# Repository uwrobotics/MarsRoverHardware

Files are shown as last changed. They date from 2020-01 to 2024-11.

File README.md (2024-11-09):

# University of Waterloo Mars Rover Hardware Repository

## Getting Started

1. Download free student license from [Altium](https://www.altium.com/solutions/academic-programs/student-licenses)
2. Download [Saturn PCB Toolkit](http://www.saturnpcb.com/pcb_toolkit/)

## Best Practices and Tips
- Preface your commit message with the project name in all caps. For example "ARM: add TVS diode" or "LIBRARY: add 10K 0603 resistor"
- When modifying the libraries, notify the #ee-git Discord channel 
- Please read this article on writing good commit messages: https://chris.beams.io/posts/git-commit/

## System Block Diagram
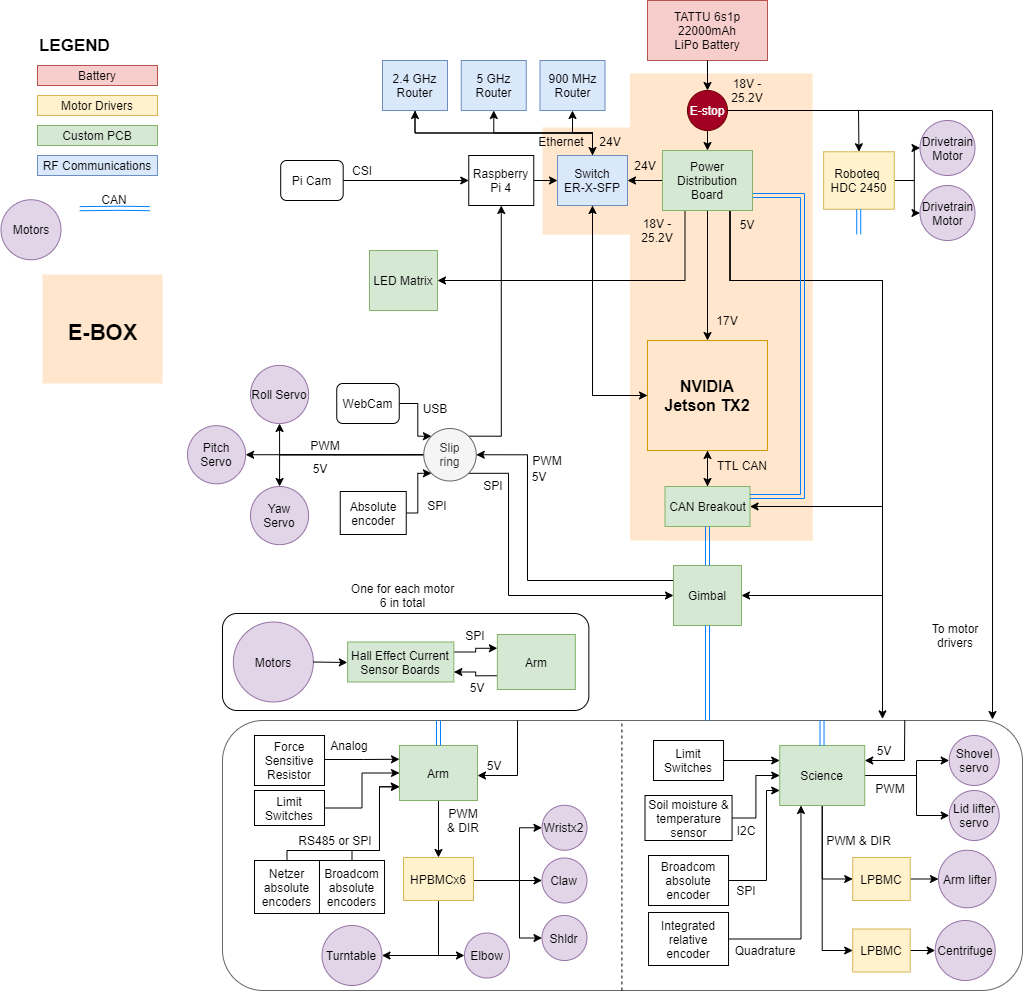
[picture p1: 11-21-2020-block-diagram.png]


#TODO: UPDATE THIS DOCUMENT
test

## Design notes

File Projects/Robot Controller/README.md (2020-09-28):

# Robot Controller

The new Robot Controller board(s) will be responsible for replacing the XBox360 Controller currently used to control the rover. As it stands now, the current plans are to design 3 boards which will each control certain modules of the rover, and can be connected/disconnected at any time. A Dev Board has been created in order to test out different control components and see which are preferred. The MCU which will be on each board is the [STM32F446RET6](https://www.st.com/resource/en/datasheet/stm32f446re.pdf).

## Block Diagram

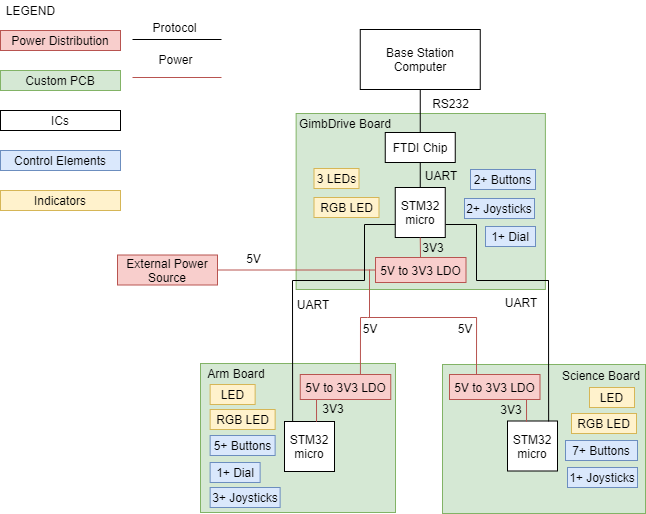
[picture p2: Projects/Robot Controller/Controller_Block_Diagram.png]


## Contributors

* **Christopher Arjune** - *Schematic Design* - [ChristopherA057](https://github.com/ChristopherA057)
* **Qinyang Bao** - *Schematic Design* - [Q7bao](https://github.com/qinyang-bao)

## Built With

* [Altium Designer](https://www.altium.com/) - PCB design software used

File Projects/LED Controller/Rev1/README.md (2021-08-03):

# LED Controller Board

The LED Controller board...

## Block Diagram

## Images

## Designers

* **Ari Wasch** - *Schematic Capture and PCB design* - [ariwasch](https://github.com/ariwasch)

## Built With

* [Altium Designer](https://www.altium.com/) - The PCB design software used

## Errata

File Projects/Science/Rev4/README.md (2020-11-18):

# Science Board

The science board is responsible for interfacing with the motors, servos, and sensors in the rover's science data collection module.
The science module consists of two primary components; the digger used to collect soil samples and the centrifuge used to mix soil samples with chemicals 
The science module will test the dampness of soil sites using the STEMMA moisture sensor to determine where to retreive soil samples.
The digger has two sub-modules the scoop and the lift.
The scoop uses the Hitec HS-82MG servo to collect soil samples.
The lift raises and lowers the scoop using a Pololu 4695.
At the top of the lift the sample into the centrifuge.
The centrifuge consists of two components; the lid and the geniva drive used to rotate the centrifuge.
The lid is controlled by the Feetech FS90 servo.
The geniva drive is driven by Pololu 4685.

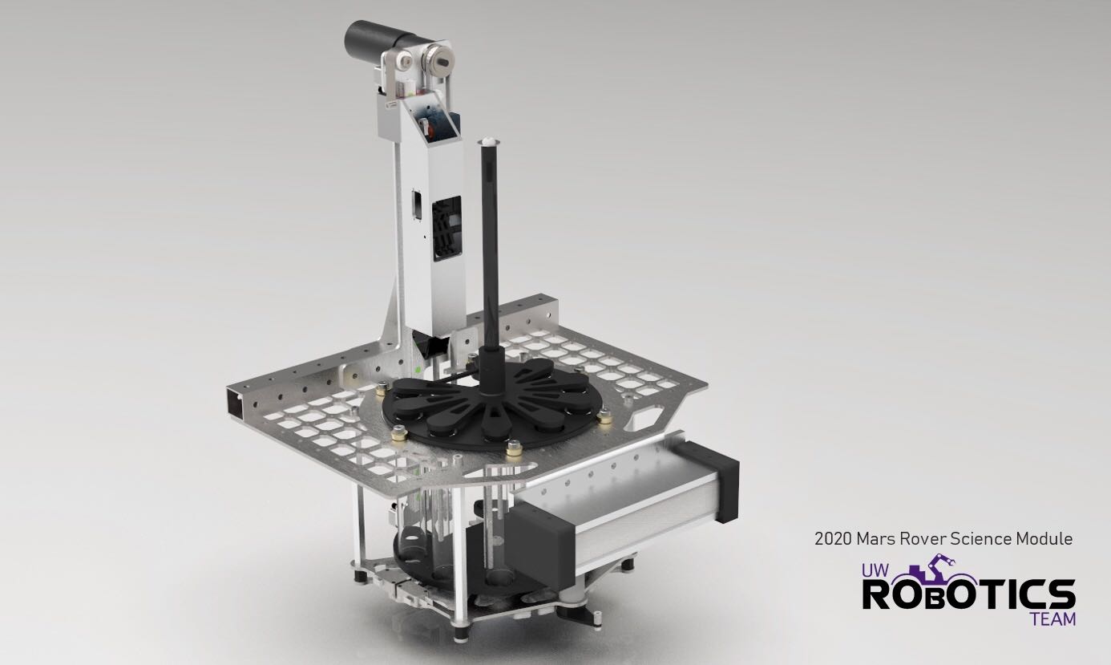
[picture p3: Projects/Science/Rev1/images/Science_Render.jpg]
Science_Render


## Block Diagram

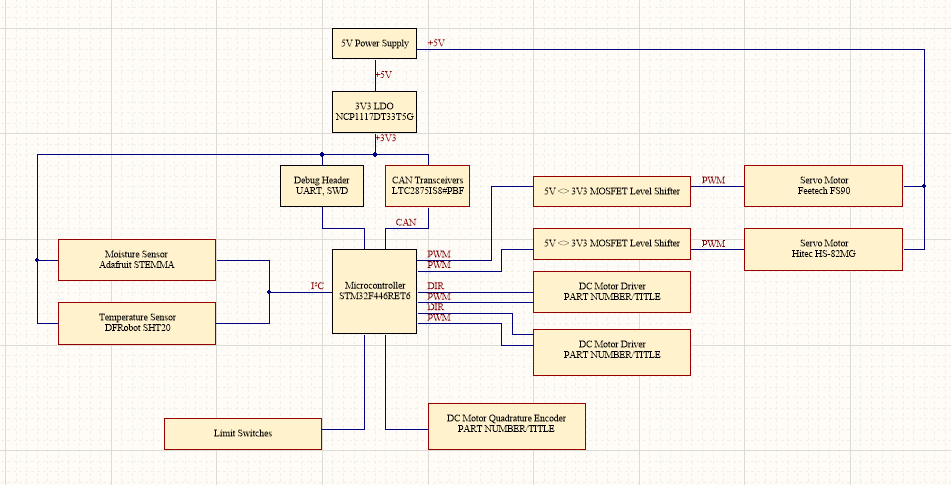
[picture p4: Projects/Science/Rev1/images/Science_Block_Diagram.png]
Block Diagram


## Actuators

### Motor Controllers

* [Cytron 10A 5-30V Dual Channel DC Motor Driver](https://www.robotshop.com/ca/en/cytron-10a-5-30v-dual-channel-dc-motor-driver.html)

### Servos

* [Feetech FS90](https://www.pololu.com/product/2818) - 9g analog servo
* [Hitec HS-82MG](https://hitecrcd.com/products/servos/micro-and-mini-servos/analog-micro-and-mini-servos/hs-82mg/product) - Metal gear micro servo 

### Motors

* [Pololu 4693 motor](https://www.pololu.com/product/4693)
* [Pololu 4685 motor](https://www.pololu.com/product/4685)

## Sensors

* [Adafruit STEMMA Soil Sensor](https://www.adafruit.com/product/4026) - I2C capacitive moisture sensor

## Images

## Designers

* **Wolfgang Windholtz** - *Schematic and PCB design* - [WolfgangWindholtz](https://github.com/WolfgangWindholtz)

## Built With

* [Altium Designer](https://www.altium.com/) - The PCB design software used

## Errata

* TBD

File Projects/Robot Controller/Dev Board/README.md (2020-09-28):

# Robot Controller - Dev Board

The Robot Controller Dev Board was created for the purpose of testing various possible components for the real Robot Controller, as well as various subsystems like power delivery and serial communication over USB. Some components on the board include joysticks, buttons, switches, and potentiometers. The MCU used on the board is the [STM32F446RET6](https://www.st.com/resource/en/datasheet/stm32f446re.pdf).

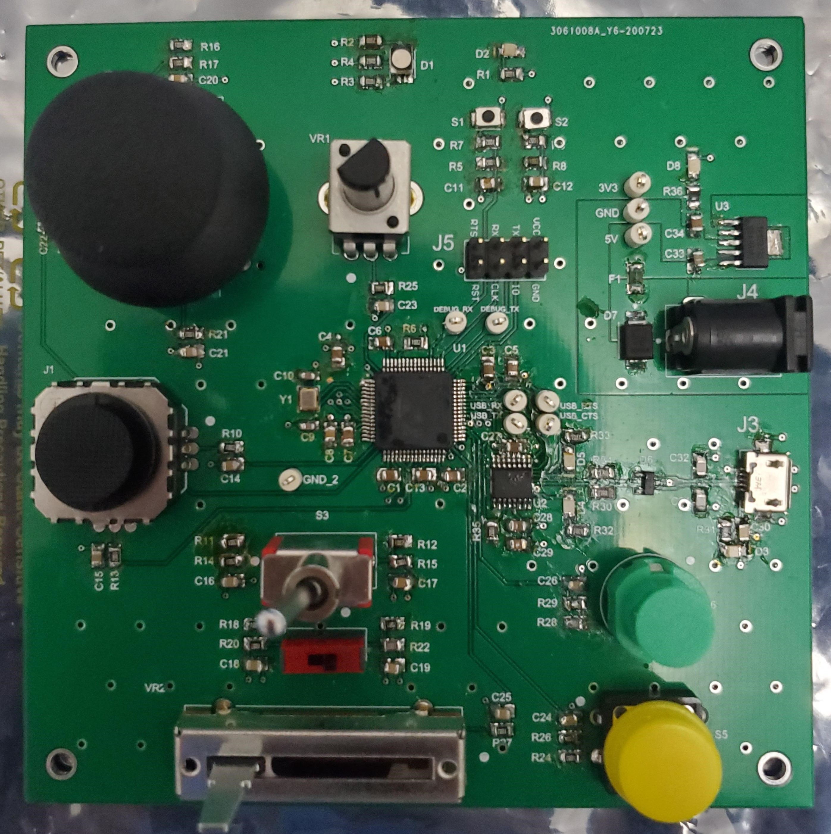
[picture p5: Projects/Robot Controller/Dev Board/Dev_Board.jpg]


## Peripherals

### Joysticks

* [COM-09032 Joystick](https://www.sparkfun.com/products/9032) - 10 kOhm 2-Axis Joystick (PS2-Style)
* [2765 Mini Joystick](https://www.adafruit.com/product/2765) - 10 kOhm 2-Axis Joystick (PSP-Style)

### Buttons

* [COM-10302 Buttons](https://www.sparkfun.com/products/10302) - 12 Tactile Buttons
* [D6R50 F2 Button](https://www.digikey.ca/en/products/detail/c-k/D6R50-F2-LFS/1466350) - Tactile Button

### Switches

* [SPDT Switch](https://www.digikey.ca/en/products/detail/e-switch/100SP1T1B4M2QE/378824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) - Toggle SPDT Switch
* [Mini SPDT Switch](https://www.digikey.ca/en/products/detail/nkk-switches/SS12SDP2/1014829) - Toggle SPDT Switch (but smaller)

### Potentiometers

* [Rotary Potentiometer](https://www.digikey.ca/en/products/detail/bourns-inc/PTV09A-4020F-B103/3534181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) - 10 kOhm Potentiometer (Rotary)
* [Slide Potentiometer](https://www.digikey.ca/en/products/detail/bourns-inc/PTA2043-2015DPB103/3781179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) - 10 kOhm Potentiomer (Slide)

## Contributors

* **Christopher Arjune** - *Schematic Design* - [ChristopherA057](https://github.com/ChristopherA057)
* **Qinyang Bao** - *Schematic Design* - [Q7bao](https://github.com/qinyang-bao)

## Built With

* [Altium Designer](https://www.altium.com/) - PCB design software used

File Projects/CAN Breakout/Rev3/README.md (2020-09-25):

# CAN Breakout Board

This board is resonsible for...

## Block Diagram

## Peripherals

## Images

## Designers

* **Qinyang Bao** - *Schematic and PCB Design* - [qinyang-bao](https://github.com/qinyang-bao)
* **Christopher Arjune** - *Schematic and PCB Design* - [ChristopherA057](https://github.com/ChristopherA057)

## Built With

* [Altium Designer](https://www.altium.com/) - The PCB design software used
* [OSHStencils](https://www.oshstencils.com/) - The PCB stencil maker used

## Errata

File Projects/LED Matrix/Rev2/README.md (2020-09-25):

# LED Matrix

This board is resonsible for...

## Block Diagram

## Peripherals

### LED 

### MOSFETs

## Images

## Designers

* **Emily Adam** - *Schematic and PCB Design* - [adamemily](https://github.com/adamemily)

## Built With

* [Altium Designer](https://www.altium.com/) - The PCB design software used
* [OSHStencils](https://www.oshstencils.com/) - The PCB stencil maker used

## Errata

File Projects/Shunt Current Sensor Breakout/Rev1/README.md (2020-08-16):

# Current Sensor Board

The current sensor board is used to ensure the measured device is operating under optimal conditions and to detect erroneous behaviour to protect components.

## Current Sensor 

* [Texas Instruments INA226](https://www.ti.com/product/INA226) - 36V, 16-bit, ultra-precise i2c output current/voltage/power monitor w/alert

## Images
Assembled PCB:
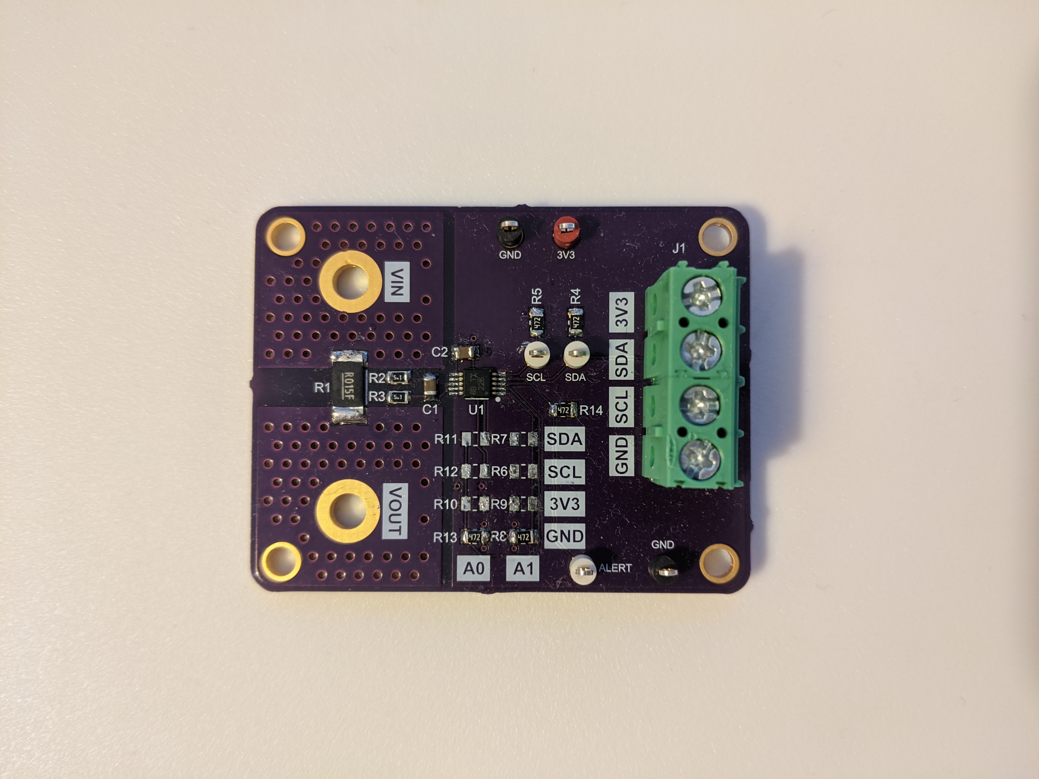
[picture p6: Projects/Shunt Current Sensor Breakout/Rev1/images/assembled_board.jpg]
Assembled PCB


## Designers

* **Noah Chapman** - *Schematic capture and PCB design* - [Nzyme](https://github.com/Nzyme)
* **Kyle Hong** - *PCB design* - [Scotrus](https://github.com/Scotrus)

## Built With

* [Altium Designer](https://www.altium.com/) - The PCB design software used

## Errata

* TBD

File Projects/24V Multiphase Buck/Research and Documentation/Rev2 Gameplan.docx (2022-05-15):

# Multiphase Buck Game Plan

## Problems/Changes

- IC power dissipation is too high
  - Can relieve this by either going down to 1 FET and a slightly lower frequency
  - Or by using a FET with a lower QGate
- Thermal reliefs on small passives are too thick
- Add in a way to break open each channel to measure output current
- Currently IC power losses may be making up the majority of power losses on the board.
- New FET – should only need one, place footprints for two
- New output caps – need low ESR ceramic
  - Need to be stable at intended temperature and frequency
  - Check temperature rise due to self heating by calculating capacitor rms current
- Double check all datasheet calculations
- Re-do datasheet calculations with specs from components where applicable (output caps, input caps, inductor)
- Find the MAX whatever layout guidelines/example for this IC – Think it was for the evaluation kit version.
- Add a polygon on some layer under the IC for thermal dissipation
- Buy a hotplate

## Testing

- Still need to test full load regulation
- Should test ripple across full range of loads
- Should test transient with larger change in load
- Overcurrent and overvoltage protection

## Current Performance

Parameter | Target | Current | Causes/Changes
Line Regulation | <0.1% | <0.04% | None
Load Regulation | | <0.3%
Output Ripple | 25mV | 304mV | Output caps or Inductor
Transient Response | | 0.625V;425us

## Improvements

- Load Regulation: reduce resistance of high-power traces – make em’ fat
- Ripple Voltage (Double check data sheet calculations):
  - More output capacitance
  - Higher switching frequency
  - Reduce inductor impedance in high-frequency operation
  - Reduce output capacitor impedance in high frequency operation
    - NPo capacitor
  - Reduce the switching-node voltage spike.
    - Adding a bootstrap resistor in series or an RC snubber circuit
  - If the output current is large, then go for a ferrite or inductor to induce more damping into the self-resonance.
  - Second stage output filter (LC filter) with low ESR output capacitors
    - Need to make sure sense lines are to the left of the LC filter so the sense lines are not disrupted by the filter
    - The corner frequency can’t be too low
    - Small inductance
  - Consider switching out electrolytics for ceramic (see data sheet)
  - Low ESR ceramic capacitors are the easiest way to reduce output ripple
    - ESR inhibits a capacitor’s ability to quickly sink or source charge

## Take Aways/Actionable from Common Mistakes Doc

- Double check compensation loop calculations/design
- Double check soft start

## To-Do

1. Research which areas need improvement and outline steps which can be taken do improve them.
2. Learn what the compensation loop does and how it impacts transient response.
3. Learn what factors affect transient responses, what are the benefits and draw backs of having a faster vs. slower transient response and how to make those changes.

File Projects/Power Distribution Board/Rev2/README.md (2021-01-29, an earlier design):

# Power Distribution Board

The Power Distribution Board takes as input 24V power from a 6s1p battery pack and supplies 24V power to the ethernet switch, 17V power to the Nvidia Jetson board, and 5V power to custom PCBs onboard the Mars rover robot. 

DC power conversion is carried out through a buck-boost converter for 24V and buck converters for 17V and 5V. Battery reverse polarity protection is achieved through an ideal diode controller and external N-channel MOSFET. Each load is controlled by a high-side smart switch with open-load detection and current limiting capabilities. 

The PDB also serves to control the LED Matrix board and interface with four URM04 ultrasonic sensors placed at the four corners of the rover to detect close-range obstacles.

## Block Diagram

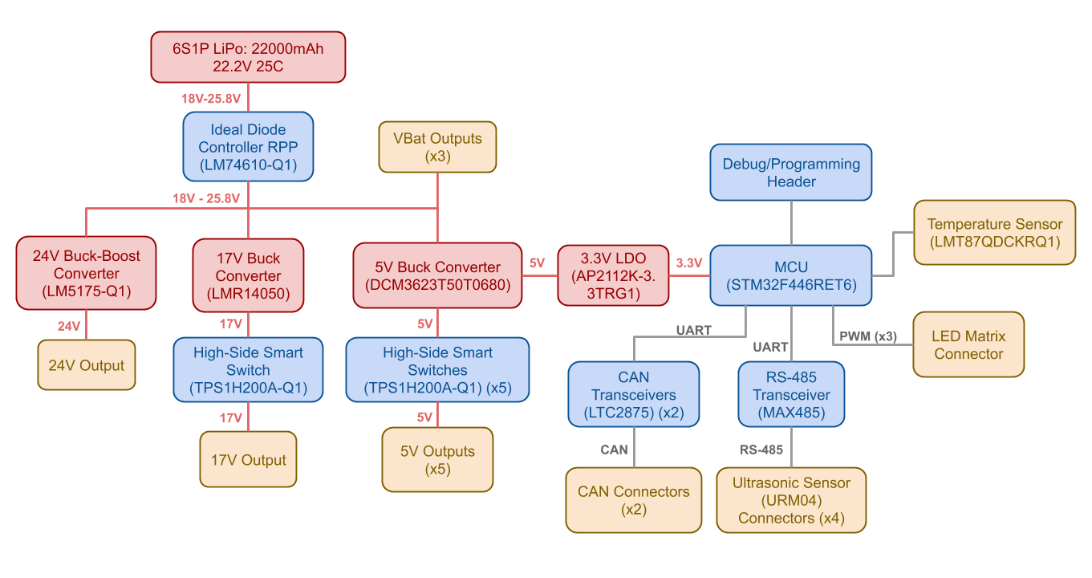
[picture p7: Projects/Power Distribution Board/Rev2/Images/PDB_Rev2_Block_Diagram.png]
Block Diagram


## Ultrasonic Sensors

* [SEN0002 URM04 V2.0](https://wiki.dfrobot.com/URM04_V2.0__SKU_SEN0002_)

## Images

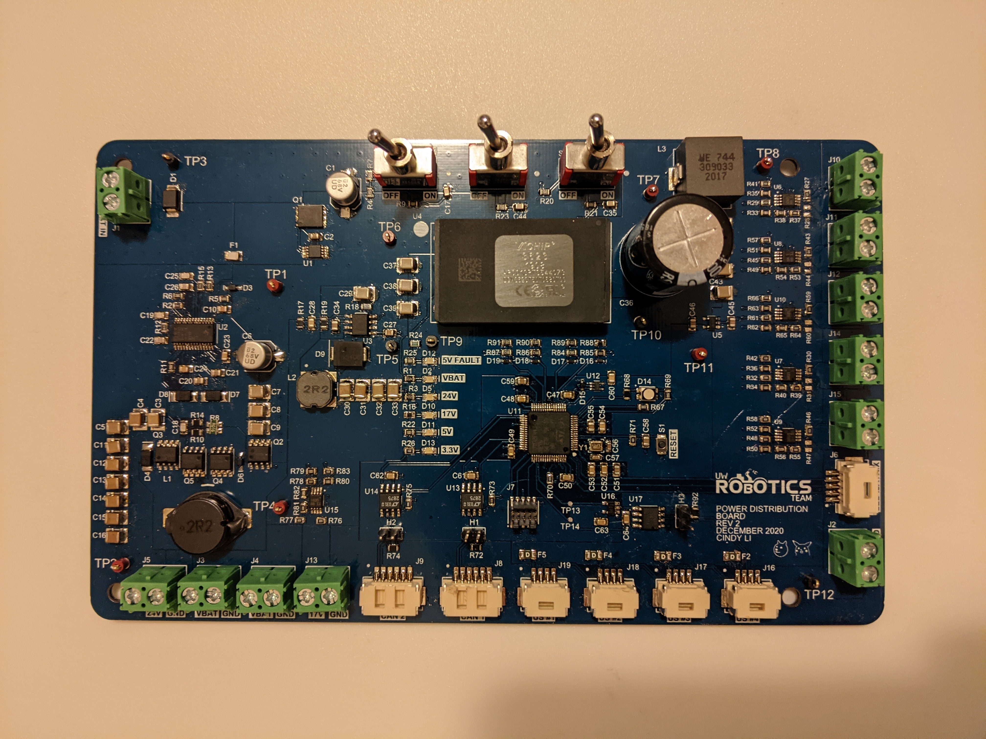
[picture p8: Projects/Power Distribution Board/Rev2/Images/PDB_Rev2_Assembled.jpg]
Assembled PCB


## Designers

* **Cindy Li** - *Schematic Capture and PCB design* - [cindyli-13](https://github.com/cindyli-13)

## Built With

* [Altium Designer](https://www.altium.com/) - The PCB design software used

## Errata

* Introduce enable signals to load switches
* Add line driver / receiver control signal to MAX485 transceiver
* Fix test point silkscreen labels
* Fix 24V buck-boost issue

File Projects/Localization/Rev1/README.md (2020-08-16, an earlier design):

# Localization Board

The localization board consists of an IMU sensor and a GPS receiver for robot localization purposes.

## Block Diagram
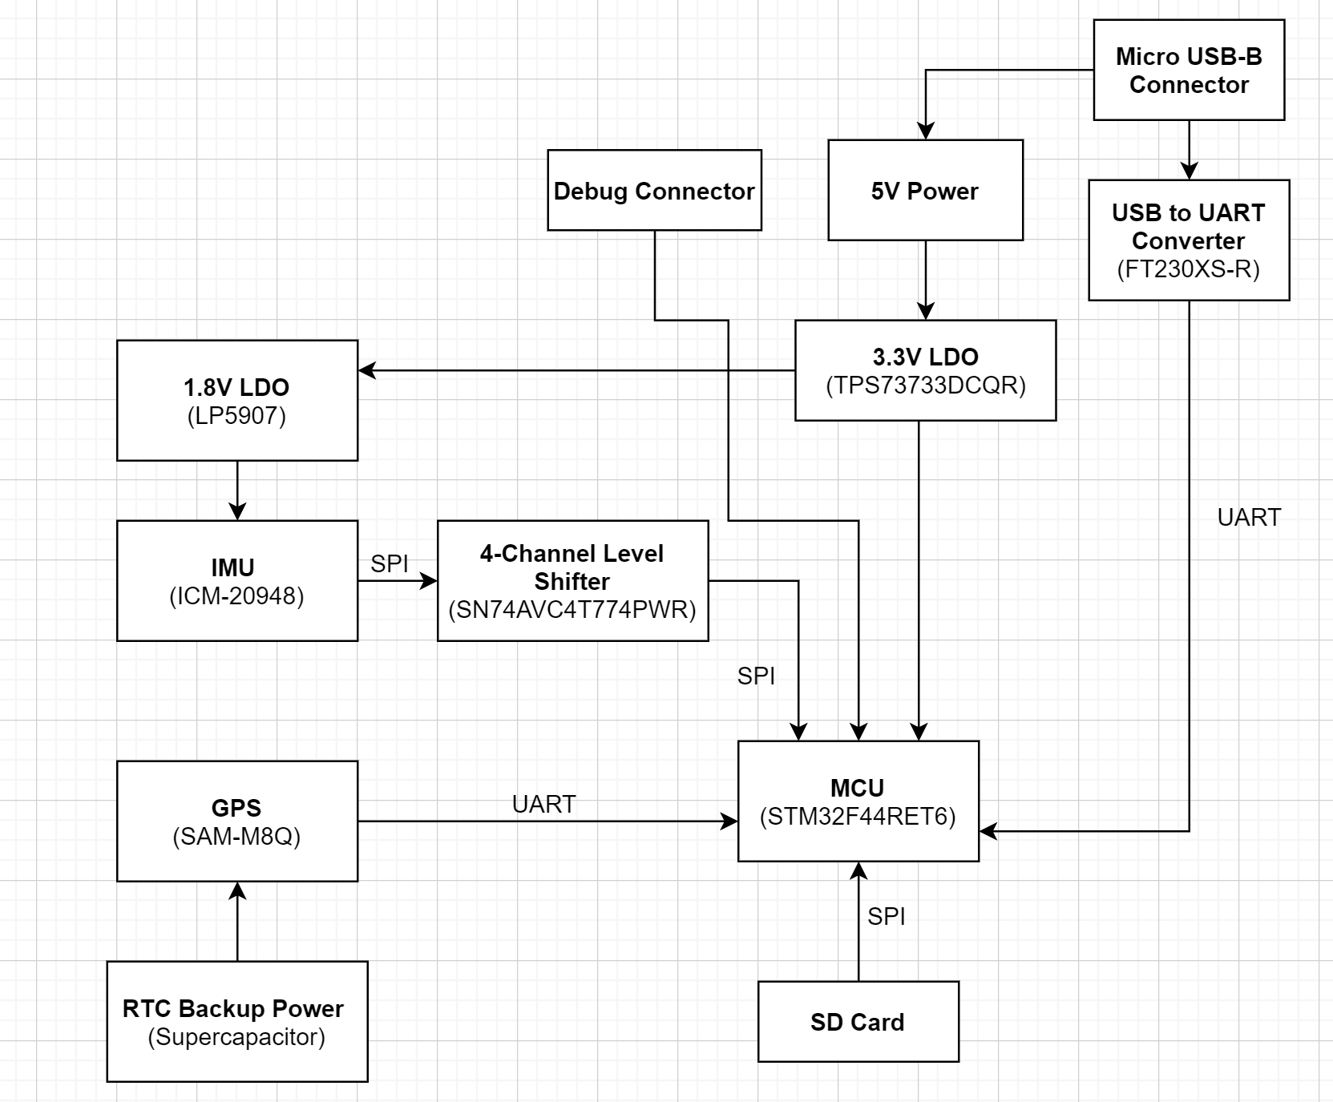
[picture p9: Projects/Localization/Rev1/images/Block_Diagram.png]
Block Diagram


## IMU
* [ICM-20948](https://invensense.tdk.com/wp-content/uploads/2016/06/DS-000189-ICM-20948-v1.3.pdf) - 9DOF IMU with Digital Motion Processor

## GPS
* [SAM-M8Q](https://www.u-blox.com/sites/default/files/SAM-M8Q_DataSheet_%28UBX-16012619%29.pdf) - u-Blox GNSS antenna module

## Images
Assembled PCB:
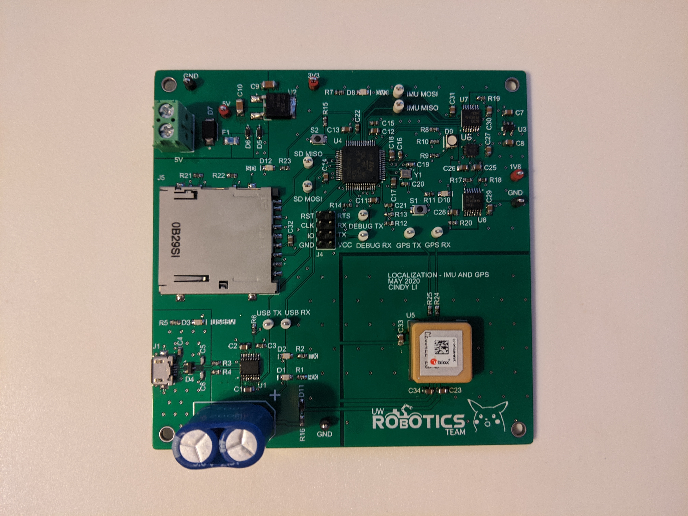
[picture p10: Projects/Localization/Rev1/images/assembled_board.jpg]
Assembled PCB


## Contributors

* **Cindy Li** - *Schematic Capture and PCB Design* - [cindyli-13](https://github.com/cindyli-13)
* **Alaina Hansen** - *Schematic Capture* - [alainahansen](https://github.com/alainahansen)

## Built With
* [Altium Designer](https://www.altium.com/) - PCB design software used

## Errata
* Add central thermal pad to ICM-20948 IMU footprint
* Tent vias

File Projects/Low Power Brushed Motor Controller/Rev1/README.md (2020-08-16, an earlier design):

# Low Power Brushed Motor Controller Board

Motor controller board for low power brushed DC motors (12V).

## Motor Driver IC
* [VNH7070AS](https://www.digikey.ca/product-detail/en/stmicroelectronics/VNH7070ASTR/497-17630-1-ND/7691023)
    * Output current: 15A
    * Maximum supply voltage: 38V 

## Motors

* [12V 131:1 Gear Motor w/Encoder](https://www.robotshop.com/en/12v-1311-gear-motor-encoder.html#Specifications)
* [Heavy Duty Rod Actuators](https://www.firgelliauto.ca/collections/400lbs-to-1000lbs/products/heavy-duty)
* [30:1 Metal Gearmotor 37Dx68L mm 12V with 64 CPR Encoder](https://www.pololu.com/product/4752)

## Reverse Polarity Protection
The reverse polarity protection circuit uses a P-channel MOSFET (or PMOS) which conducts current when the applied gate voltage is high and does not conduct when the applied gate voltage is low. In the case that the 12V and GND references are reversed, a high voltage level is experienced at the gate, causing the PMOS to switch off and act as an open circuit.

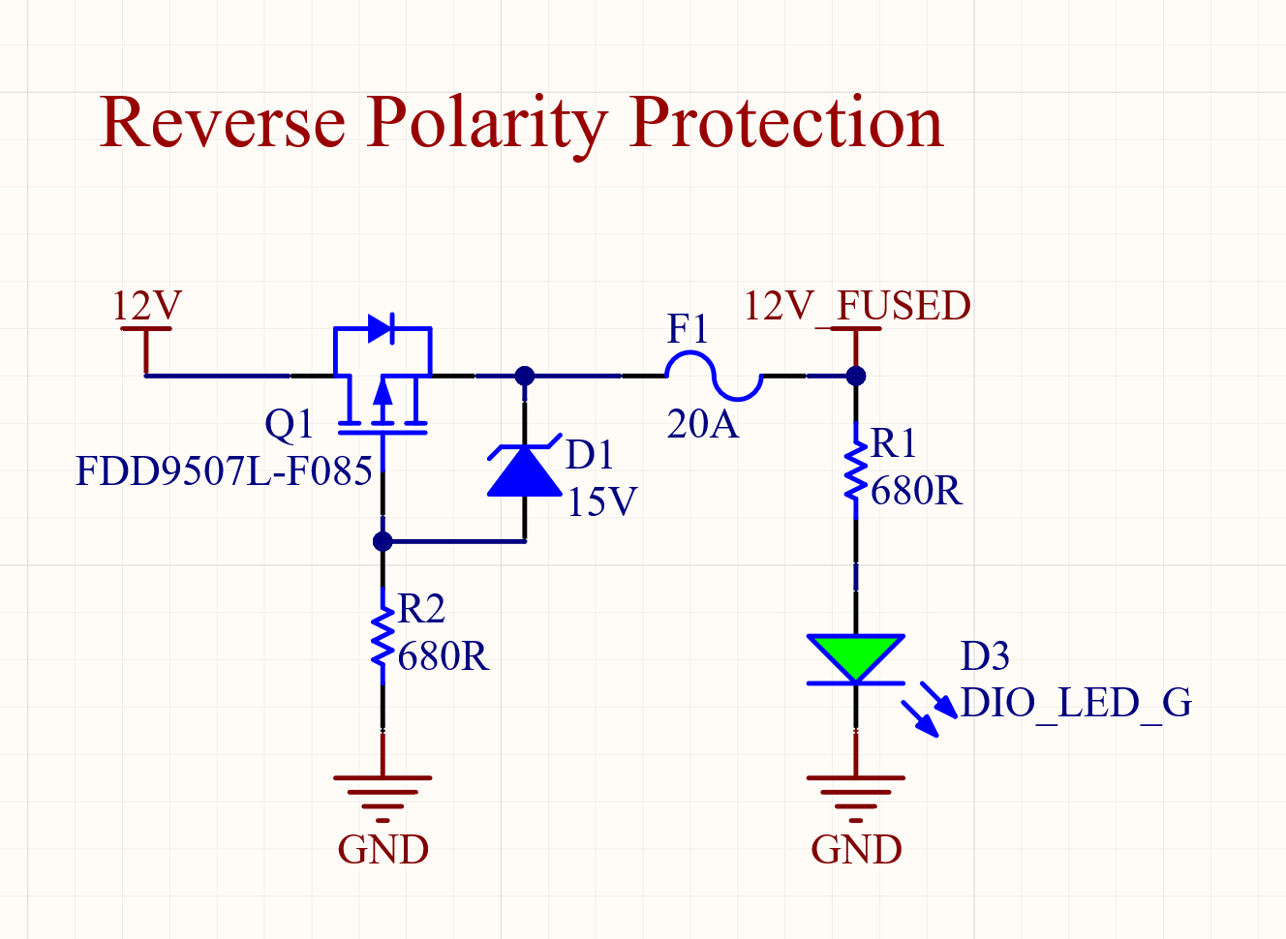
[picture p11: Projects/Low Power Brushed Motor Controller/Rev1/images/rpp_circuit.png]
Reverse Polarity Protection Circuit


## Images
Assembled PCB:
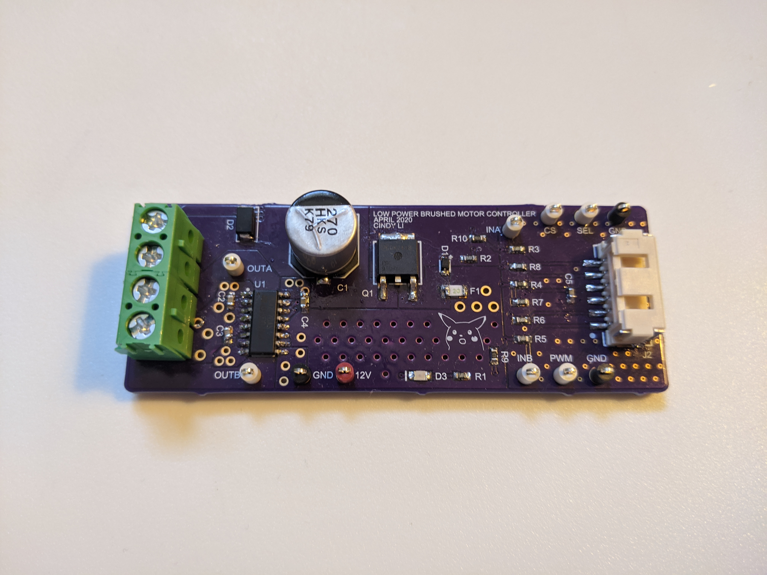
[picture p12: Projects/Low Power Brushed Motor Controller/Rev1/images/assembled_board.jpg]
Assembled PCB


## Contributors

* **Kyle Hong** - *Schematic Capture* - [Scotrus](https://github.com/Scotrus)
* **Cindy Li** - *PCB Design* - [cindyli-13](https://github.com/cindyli-13)

## Built With

* [Altium Designer](https://www.altium.com/) - PCB design software used

## Errata
* Fix P-Channel MOSFET footprint
* Tent vias

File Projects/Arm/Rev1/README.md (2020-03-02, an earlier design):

# Arm Board

The arm board is responsible for the control of the rover's 6-DOF robotic arm. The MCU onboard is the [STM32F446VET7](https://www.st.com/resource/en/datasheet/stm32f446re.pdf). This PCB interfaces with force sensitive resistor, servo motor, linear actuator, three brushed DC motor drivers, three absolute encoders, three relative integrated encoders, and ten limit switches.
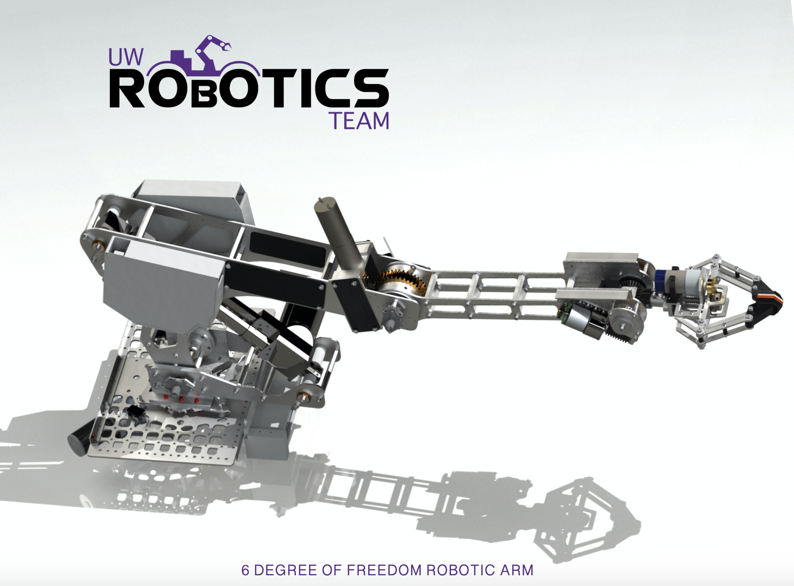
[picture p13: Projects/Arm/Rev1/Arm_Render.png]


## Block Diagram

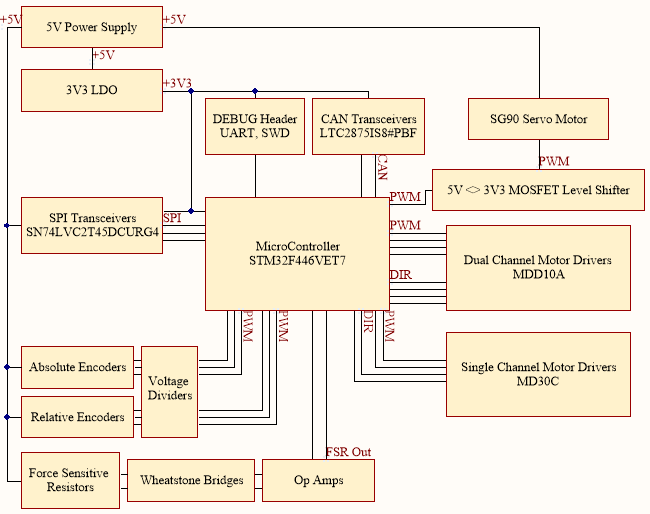
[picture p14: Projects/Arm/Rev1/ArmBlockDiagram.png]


## Peripherals

### Motor Controllers

* [Cytron MDD10A](https://www.cytron.io/p-10amp-5v-30v-dc-motor-driver-2-channels) - 10Amp 5V-30V Dual Channel DC Motor Driver
* [Cytron MD30C](https://www.cytron.io/p-30amp-5v-30v-dc-motor-driver) - 30Amp 5V-30V DC Motor Driver

### Servo

* [SG90](http://www.ee.ic.ac.uk/pcheung/teaching/DE1_EE/stores/sg90_datasheet.pdf) - Micro servo motor

### Limit Switches

* [Twidec Limit Switch](https://www.amazon.ca/gp/product/B07NVDXGPS/ref=ppx_yo_dt_b_search_asin_title?ie=UTF8&psc=1) - Short Hinge Roller Lever Arm Switch
* [Cylewet Limit Switch](https://www.amazon.ca/gp/product/B07DGX5Q1Q/ref=ppx_yo_dt_b_search_asin_title?ie=UTF8&psc=1) - Long Straight Hinge Lever Arm Switch

### Force Sensitive Resistor

* [Interlink Electronics FSR 402](https://cdn.sparkfun.com/assets/8/a/1/2/0/2010-10-26-DataSheet-FSR402-Layout2.pdf) - 18.28mm diameter force sensitive resistor

### Encoders

* [US Digital MAE3](https://www.usdigital.com/products/encoders/absolute/magnetic/MAE3) - Absolute magnetic kit encoder with PWM output. 10/12 bit
* [Broadcom AEAT-6012-A06](https://www.broadcom.com/products/motion-control-encoders/magnetic-encoders/aeat-6012-a06) - 12-bit magnetic encoder with SPI output

## Images

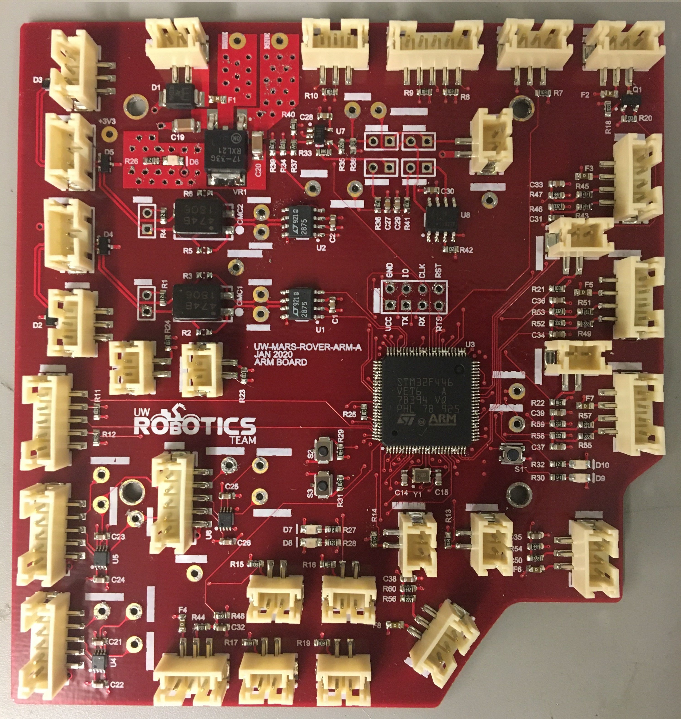
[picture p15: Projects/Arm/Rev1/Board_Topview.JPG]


## Contributors

* **Kyle Hong** - *PCB design* - [Scotrus](https://github.com/Scotrus)
* **Princely Onaifo** - *MCU config and routing* - [Princely-O](https://github.com/Princely-O)
* **Noah Chapman** - *SPI encoder circuit* - [Nzyme](https://github.com/Nzyme)
* **Ayesha Ebrahim** - *Force sensitive resistor circuit* - [a-ebrahim](https://github.com/a-ebrahim)

## Built With

* [Altium Designer](https://www.altium.com/) - PCB design software used
* [OSHStencils](https://www.oshstencils.com/) - PCB stencil maker used
* [Candor Industries](https://www.candorind.com/) - PCB sponsor

## Errata

* Configure and route two shoulder limit switches for Rev 2
* Remove low pass filtering capacitor from encoder output
* Replace all 0603 fuses with 1206 fuses

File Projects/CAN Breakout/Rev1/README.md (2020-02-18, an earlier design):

# CAN Breakout Board

The CAN breakout board is used to allow the NVIDIA Jetson TX2 Module to communicate to the rover's CAN bus.

## Current Sensor 

* [Analog Devices LTC2875](https://www.analog.com/media/en/technical-documentation/data-sheets/LTC2875.pdf) - ±60V Fault Protected 3.3V or 5V 25kV ESD High Speed CAN FD Transceiver

## Images

- insert top view picture of PCB

## Designers

* **Alaina Hansen** - *Schematic capture and PCB design* - [Nzyme](https://github.com/Nzyme)

## Built With

* [Altium Designer](https://www.altium.com/) - The PCB design software used

## Errata

* TBD

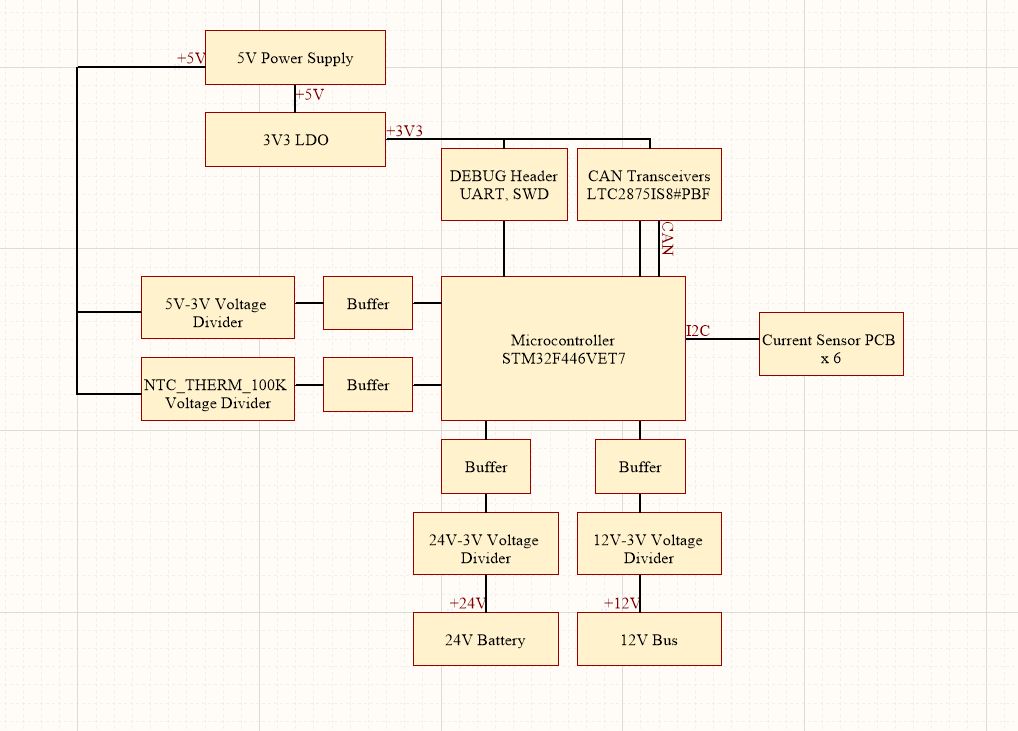
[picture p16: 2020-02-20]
Projects/Safety/Rev1/images/safety_block_diagram.jpg

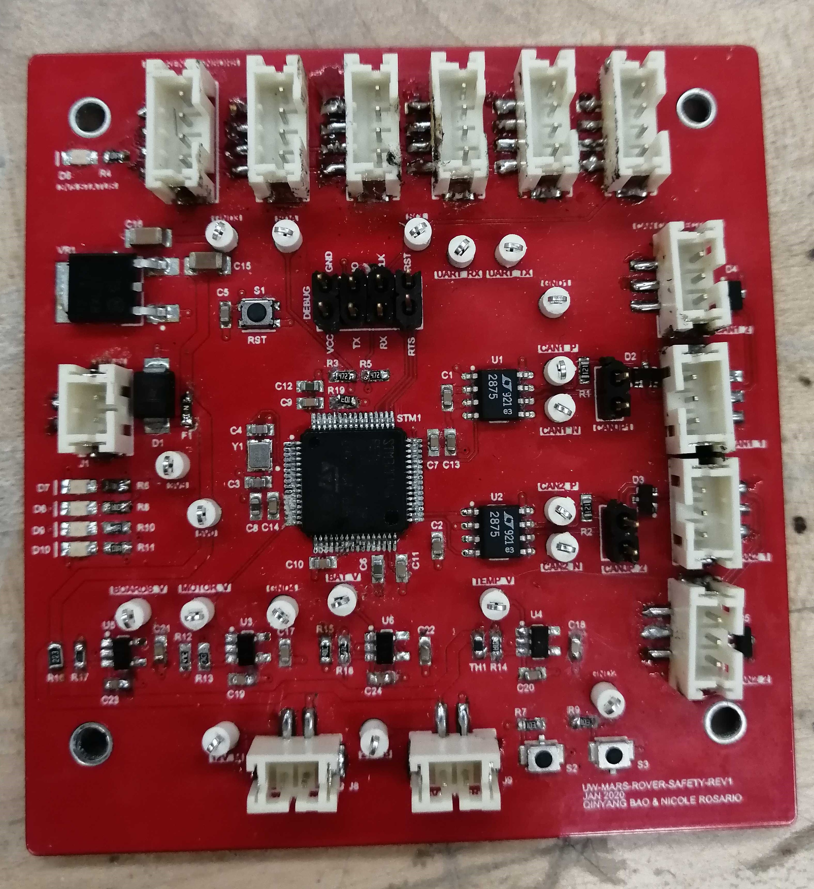
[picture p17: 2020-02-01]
Projects/Safety/Rev1/images/safety_top_view.jpg

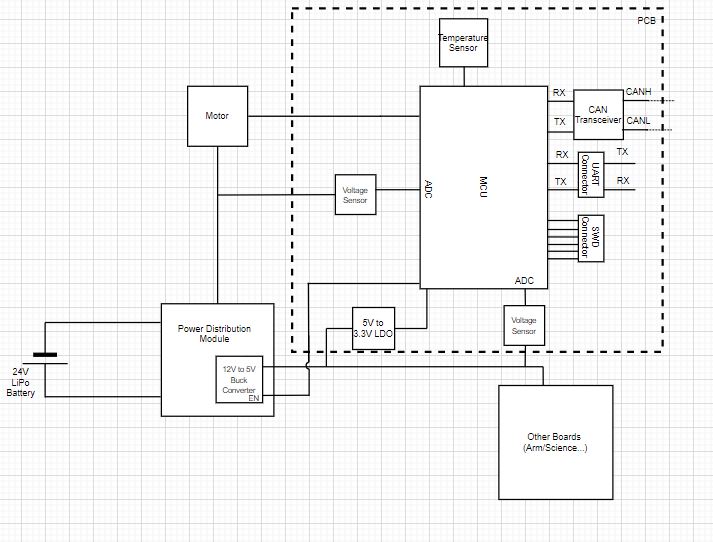
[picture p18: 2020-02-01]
Projects/Safety/Rev1/images/safety_block_diagram_drawio.jpg

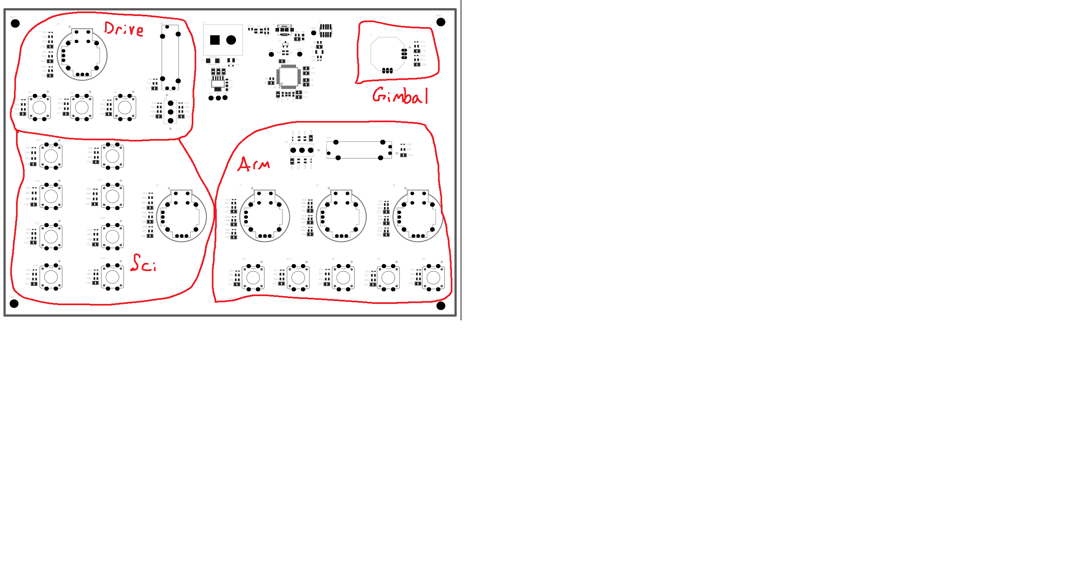
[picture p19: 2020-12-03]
Projects/Robot Controller/Rev1/Control Grouping.png

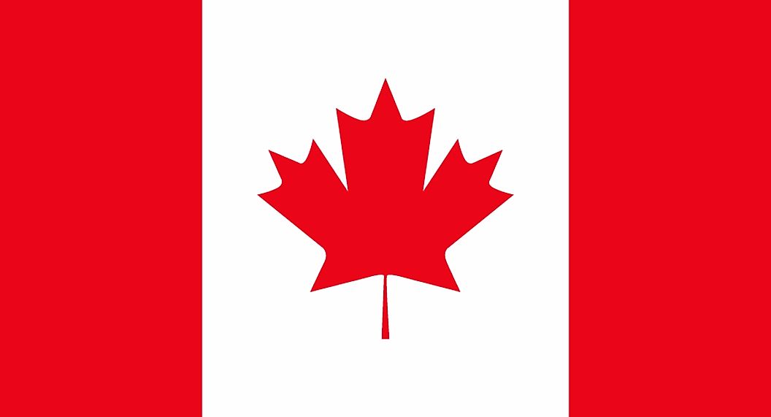
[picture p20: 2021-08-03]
Templates/Canada Flag.jpg

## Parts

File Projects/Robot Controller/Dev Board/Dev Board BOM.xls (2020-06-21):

Line # | Name | Description | Designator | Quantity | Manufacturer 1 | Manufacturer Part Number 1 | Manufacturer Lifecycle 1 | Supplier 1 | Supplier Part Number 1 | Supplier Unit Price 1 | Supplier Subtotal 1
 | MOUNTING_HOLES | 6cm x 6cm | MH1, MH2, MH3, MH4 | 4
 |  | CAP CER 4.7UF 16V X5R 0805 | C29 | 1 | Samsung | CL21A475KOFNNNE | Not Recommended for New Design | Digi-Key | 1276-1065-1-ND | 0.35179 | 0.35179
 | CAP_4.7uF_16V_0805 | CAP CER 4.7UF 16V X5R 0805 | C5, C13 | 2 | Samsung | CL21A475KOFNNNE | Not Recommended for New Design | Digi-Key | 1276-1065-1-ND | 0.35179 | 0.70357
 |  | CAP CER 47PF 100V NPO 0805 | C31, C32 | 2 | Yageo | AC0805JRNPO0BN470 | Unknown | Digi-Key | 311-3131-1-ND | 0.25853 | 0.51707
 |  | CAP CER 10000PF 16V X7R 0805 | C30 | 1 | Yageo | AC0805KRX7R7BB103 | Unknown | Digi-Key | 311-3161-1-ND | 0.27214 | 0.27214
 | 2_AXIS_JOYSTICK | JOYSTICK 10K OHM 2 AXIS TH | J2 | 1 | SparkFun | 9032 | Unknown | Digi-Key | 1568-1526-ND | 5.37 | 5.37
 | FUSE_1.25A_1206 | FUSE SMD 1.25A 63V | F1 | 1 | Littelfuse | 04661.25NRHF | Unknown | Digi-Key | F11418CT-ND | 1.14 | 1.14
 | Pushbutton | Momentary Switch (Pushbutton) - SPST | S5 | 1 | SparkFun | COM-10302 | Unknown | Digi-Key | 1568-1332-ND | 7.96 | 7.96
 | TESTPOINT_LOOP | Loop testpoint through-hole pad | TP1, TP2, TP3, TP4, TP5, TP6, TP7, TP8, TP9, TP10 | 10 | Permabond | 5002 | Unknown | Digi-Key | 36-5002-ND | 0.45583 | 4.56
 |  | CAP CER 1UF 25V X7R 0805 | C33, C34 | 2 | Murata | GCM21BR71E105KA56K | Volume Production | Digi-Key | 490-14743-1-ND | 0.46264 | 0.92528
 | 0.1μF | CAP CER 0.1UF 50V X7R 0805 | C1, C2, C3, C4, C6, C7 | 6 | Murata | GCD21BR71H104KA01L | Volume Production | Digi-Key | 490-11955-1-ND | 0.51842 | 3.11
 | 0.1μF | CAP CER 0.1UF 50V X7R 0805 | C27, C28 | 2 | Murata | GCD21BR71H104KA01L | Volume Production | Digi-Key | 490-11955-1-ND | 0.51842 | 1.04
 | 1kΩ | RES SMD 1K OHM 1% 1/8W 0805 | R31, R32, R33 | 3 | Yageo Phycomp | RC0805FR-071KL | Volume Production | Digi-Key | 311-1.00KCRCT-ND | 0.13607 | 0.40821
 | 2_AXIS_JOYSTICK_SMALL | JOYSTICK 10K OHM 2 AXIS TH | J1 | 1 | Adafruit Industries | 2765 | Volume Production | Digi-Key | 1528-1730-ND | 3.4 | 3.4
 | 120 | RES SMD 120 OHM 1% 1/8W 0805 | R36 | 1 | Vishay | CRCW0805120RFKEA | Volume Production | Digi-Key | 541-120CCT-ND | 0.13607 | 0.13607
 | 629105136821 | Micro USB 2.0 Type B Receptacle WR-COM, Horizontal, SMT, with Pads and Pegs | J3 | 1 | Wurth Electronics | 629105136821 | Volume Production | Digi-Key | 732-3155-1-ND | 1.65 | 1.65
 | CAP_1uF_16V_0805 | CAP CER 1UF 16V X7R 0805 | C8, C11, C12, C14, C15, C16, C17, C18, C19, C20, C21, C22, C23, C24, C25, C26 | 16 | Yageo | CC0805KKX7R7BB105 | Volume Production | Digi-Key | 311-1365-1-ND | 0.17689 | 2.83
 | CL10C140JB8NNNC | Cap Ceramic 14pF 50V C0G 5% SMD 0603 125C Cardboard T/R | C9, C10 | 2 | Samsung | CL10C140JB8NNNC | Volume Production | Digi-Key | 1276-2187-1-ND | 0.13607 | 0.27214
 | CRYSTAL_25MHZ | CRYSTAL 25.0000MHZ 12PF SMD | Y1 | 1 | Kyocera AVX | CX2520DB25000H0FLJC1 | Volume Production | Digi-Key | 1253-1724-1-ND | 0.9797 | 0.9797
 | HEADER 4X2 | CONN HEADER VERT 8POS 2.54MM | J5 | 1 | Harwin | M20-9980445 | Volume Production | Digi-Key | 952-2122-ND | 0.48985 | 0.48985
 | IC_USB_TRANSCEIVER |  | U2 | 1 | FTDI | FT230XS-R | Volume Production | Digi-Key | 768-1135-1-ND | 2.78 | 2.78
 | LED_RGB | LED RGB DIFFUSED 4PLCC SMD | D1 | 1 | Broadcom | ASMB-MTB1-0A3A2 | Volume Production | Digi-Key | 516-3280-1-ND | 0.78921 | 0.78921
 | LG R971-KN-1 | LED GREEN DIFFUSED 0805 SMD | D2, D4, D8 | 3 | Osram Opto | LGR971-KN-1 | Volume Production | Digi-Key | 475-1410-1-ND | 0.35378 | 1.06
 | LS R976-NR-1 | LED RED DIFFUSED 0805 SMD | D3 | 1 | Osram Opto | LSR976-NR-1 | Volume Production | Digi-Key | 475-1278-1-ND | 0.381 | 0.381
 | LY R976-PS-36 | LED YELLOW DIFFUSED 0805 SMD | D5 | 1 | Osram Opto | LYR976-PS-36 | Volume Production | Digi-Key | 475-2560-1-ND | 0.381 | 0.381
 | MOMENTARY_SWITCH_D6R | SWITCH PUSH SPST-NO 0.1A 32V | S6 | 1 | ITT C&K | D6R50F2LFS | Volume Production | Digi-Key | 401-1993-ND | 1.5 | 1.5
 | PJ-102B | 2.5 x 6.5 mm, 2.5 A, Horizontal, Through Hole, Tapered Pins, Dc Power Jack Connector | J4 | 1 | CUI | PJ-102B | Volume Production | Digi-Key | CP-102B-ND | 0.87085 | 0.87085
 | POT_10K | POT 10K OHM 1/20W CARBON LINEAR | VR1 | 1 | Bourns | PTV09A-4020F-B103 | Volume Production | Digi-Key | PTV09A-4020F-B103-ND | 1.13 | 1.13
 | POT_10K_SLIDE | SLIDE POT 10K OHM 0.1W TOP 20MM | VR2 | 1 | Bourns | PTA2043-2015DPB103 | Volume Production | Digi-Key | PTA2043-2015DPB103-ND | 1.76 | 1.76
 | RES_10kΩ_0805 | RES SMD 10K OHM 1% 1/8W 0805 | R5, R6, R7, R8, R9, R10, R11, R12, R13, R14, R15, R16, R17, R18, R19, R20, R21, R22, R23, R24, R25, R26, R27, R28, R29, R35 | 26 | Yageo | RC0805FR-0710KL | Volume Production | Digi-Key | 311-10.0KCRCT-ND | 0.05443 | 1.42
 | RES_20Ω_0805 | RES SMD 20 OHM 1% 1/8W 0805 | R2, R4 | 2 | Yageo | RC0805FR-0720RL | Volume Production | Digi-Key | 311-20.0CRCT-ND | 0.13607 | 0.27214
 | RES_27Ω_0805 | RES SMD 27 OHM 1% 1/8W 0805 | R30, R34 | 2 | Yageo | RC0805FR-0727RL | Volume Production | Digi-Key | 311-27.0CRCT-ND | 0.13607 | 0.27214
 | RES_100Ω_0805 | RES SMD 100 OHM 1% 1/8W 0805 | R1, R3 | 2 | Yageo | RC0805FR-07100RL | Volume Production | Digi-Key | 311-100CRCT-ND | 0.13607 | 0.27214
 | STM32F446RET6 | ARM Cortex-M4 32-bit MCU+FPU, 512 KB Flash, 128 KB Internal RAM, 50 I/Os, 64-Pin LQFP, -40 to 85 degC, Tray | U1 | 1 | STMicroelectronics | STM32F446RET6 | Volume Production | Digi-Key | 497-15376-ND
 | SW_SPDT | SWITCH TOGGLE SPDT 5A 120V | S3 | 1 | E-Switch | 100SP1T1B4M2QE | Volume Production | Digi-Key | EG2355-ND | 2.71 | 2.71
 | SW_SPDT_SMALL | SWITCH SLIDE SPDT 100MA 30V | S4 | 1 | NKK Switches | SS12SDP2 | Volume Production | Digi-Key | 360-2133-ND | 2.12 | 2.12
 | SW_TACTILE | Tactile Switch (Grey) | S1, S2 | 2 | Omron | B3U-1000P | Volume Production | Digi-Key | SW1020CT-ND | 1.33 | 2.67
 | TPS73733DCQR | IC REG LINEAR 3.3V 1A SOT223-6 | U3 | 1 | Texas Instruments | TPS73733DCQR | Volume Production | Digi-Key | 296-22681-2-ND | 0.76009 | 1900.22
 | TVS_DIODE_UNIDIR_5V | TVS DIODE 5V 9.2V DO214AA | D7 | 1 | Bourns | SMBJ5.0A | Volume Production | Digi-Key | SMBJ5.0ABCT-ND | 0.53067 | 0.53067
 | TVS_DIODE_USB_5.5V | ESD Suppressor Diode Arrays 8KV 3-Pin SOT-23 T/R | D6 | 1 | Texas Instruments | TPD2E009DBZR | Volume Production | Digi-Key | 296-24657-1-ND | 0.76199 | 0.76199

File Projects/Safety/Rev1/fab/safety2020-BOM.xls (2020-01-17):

Line # | Name | Description | Designator | Quantity | Manufacturer 1 | Manufacturer Part Number 1 | Manufacturer Lifecycle 1 | Supplier 1 | Supplier Part Number 1 | Supplier Unit Price 1 | Supplier Subtotal 1
 | TESTPOINT_LOOP | Loop testpoint through-hole pad | 3V3, 5V0, 12V_M, 24V_B, BAT_V, BOARDS_V, CAN1_N, CAN1_P, CAN2_N, CAN2_P, GND1, GND2, GND3, GND4, MOTOR_V, ONBOARD_TEMP_V, SCL, SDA, UART_RX, UART_TX | 20 | Permabond | 5002 | Unknown | Digi-Key | 36-5002-ND | 0.45646 | 9.13
 | CAP_0.1uF_16V_0603 | CAP CER 0.1UF 16V X7R 0603 | C1, C2, C5, C7, C9, C10, C11, C13, C17, C18, C19, C20, C21, C22, C23, C24 | 16 | Yageo | CC0603KRX7R7BB104 | Volume Production | Digi-Key | 311-1088-1-ND | 0.0626 | 1
 | CL10C140JB8NNNC | Cap Ceramic 14pF 50V C0G 5% SMD 0603 125C Cardboard T/R | C3, C4 | 2 | Samsung | CL10C140JB8NNNC | Volume Production | Digi-Key | 1276-2187-1-ND | 0.13042 | 0.26083
 | CAP_4.7uF_0603 | CAP CER 4.7UF 6.3V X5R 0603 | C6, C12 | 2 | Yageo | CC0603KRX5R5BB475 | Volume Production | Digi-Key | 311-1521-1-ND | 0.313 | 0.626
 | CAP_1uF_16V_0603 | CAP CER 1UF 16V Y5V 0603 | C8 | 1 | Yageo | CC0603ZRY5V7BB105 | Volume Production | Digi-Key | 311-1372-1-ND | 0.13042 | 0.13042
 | CAP_10nF_0603 | CAP CER 10000PF 16V X7R 0603 | C14 | 1 | Yageo | CC0603KRX7R7BB103 | Volume Production | Digi-Key | 311-3369-1-ND | 0.13042 | 0.13042
 | 10uF | CAP CER 10UF 50V X5R 1206 | C15, C16 | 2 | Murata | GRT31CR61H106KE01L | Volume Production | Digi-Key | 490-12456-1-ND | 0.92596 | 1.85
 | CON_3M_SM4 |  | CAN1_1, CAN1_2, CAN2_1, CAN2_2 | 4 | JST | B3B-PH-SM4-TB(LF)(SN) | Volume Production | Digi-Key | 455-1735-1-ND | 0.82163 | 3.29
 | JUMPER_2 | HEADER 2X1 | CANJP_1, CANJP_2 | 2 | TE Connectivity | 87220-2 | Volume Production | Digi-Key | A26542-ND | 2.09 | 4.17
 | TVS_DIODE_BIDIRECTIONAL | TVS DIODE 5V 9.2V DO214AA | D1 | 1 | Littelfuse | SMBJ5.0CA | Volume Production | Digi-Key | SMBJ5.0CALFCT-ND | 0.50863 | 0.50863
 | TVS_DIODE_CAN | TVS DIODE 24V 41V SOT323-3 | D2, D3, D4, D5 | 4 | Nexperia | PESD2CAN.215 | Unknown | Digi-Key | 1727-3891-1-ND | 0.56079 | 2.24
 | DIO_LED_G | LED GREEN DIFFUSED 0805 SMD | D6, D8, D9, D10 | 4 | Osram Opto | LGR971-KN-1 | Volume Production | Digi-Key | 475-1410-1-ND | 0.35213 | 1.41
 | DIO_LED_Y | LED YELLOW DIFFUSED 0805 SMD | D7 | 1 | Osram Opto | LYR976-PS-36 | Volume Production | Digi-Key | 475-2560-1-ND | 0.37821 | 0.37821
 | HEADER 4X2 | Header, 4-Pin Dual row | DEBUG | 1 | Sullins | GRPB042VWVN-RC | Volume Production | Digi-Key | S9015E-04-ND | 0.83467 | 0.83467
 | FUSE_2A_0603 | FUSE SMD 2A 32V | F1 | 1 | Littelfuse | 0467002.NRHF | Volume Production | Digi-Key | F7132CT-ND | 1.57 | 1.57
 | CON_2M_SM4 |  | J1, J8, J9 | 3 | JST | B2B-PH-SM4-TB(LF)(SN) | Volume Production | Digi-Key | 455-1734-1-ND | 0.71729 | 2.15
 | CON_4M_SM4 |  | J2, J3, J4, J5, J6, J7 | 6 | JST | B4B-PH-SM4-TB(LF)(SN) | Volume Production | Digi-Key | 455-1736-1-ND | 1.04 | 6.26
 | RES_120R_0603 | RES SMD 120 OHM 5% 1/10W 0603 | R1, R2 | 2 | Yageo | RC0603JR-07120RL | Volume Production | Digi-Key | 311-120GRCT-ND | 0.02478 | 0.24779
 | RES_4K7_0603 | RES SMD 4.7K OHM 5% 1/10W 0603 | R3, R5 | 2 | Yageo | RC0603JR-074K7L | Volume Production | Digi-Key | 311-4.7KGRCT-ND | 0.02478 | 0.24779
 | RES_100R_0603 | RES SMD 100 OHM 1% 1/10W 0603 | R4, R6, R8, R10, R11 | 5 | Yageo | RC0603FR-07100RL | Volume Production | Digi-Key | 311-100HRCT-ND | 0.03 | 0.29996
 | RES_10K_0603 | RES SMD 10K OHM 5% 1/10W 0603 | R7, R9, R19 | 3 | Yageo | RC0603JR-0710KL | Volume Production | Digi-Key | 311-10KGRCT-ND | 0.02478 | 0.24779
 | RES_1K_0603 | RES SMD 1K OHM 5% 1/10W 0603 | R12, R13, R14, R15, R16, R17, R18 | 7 | Yageo | RC0603JR-071KL | Volume Production | Digi-Key | 311-1.0KGRCT-ND | 0.02478 | 0.24779
 | SW_PWR | Power Switch (Red) | S1 | 1 | ITT C&K | PTS830GM140SMTRLFS | Volume Production | Digi-Key | CKN10587CT-ND | 0.66513 | 0.66513
 | SW_TACTILE | Tactile Switch (Grey) | S2, S3 | 2 | Omron | B3U-1100P | Volume Production | Digi-Key | SW1021CT-ND | 1.3 | 2.61
 | STM32F446RET6 | ARM Cortex-M4 32-bit MCU+FPU, 512 KB Flash, 128 KB Internal RAM, 50 I/Os, 64-Pin LQFP, -40 to 85 degC, Tray | STM1 | 1 | STMicroelectronics | STM32F446RET6 | Volume Production | Digi-Key | 497-15376-ND | 9.62 | 9.62
 | NTC_THERM_100K | THERM NTC 100KOHM 4700K 0603 | TH1 | 1 | Panasonic | ERT-J1VV104J | Volume Production | Digi-Key | P10555CT-ND | 0.313 | 0.313
 | IC TXRX CAN | IC TXRX CAN 4MBPS 8SO | U1, U2 | 2 | Analog Devices / Linear Technology | LTC2875IS8#PBF | Volume Production | Digi-Key | LTC2875IS8#PBF-ND | 5.43 | 10.85
 | OPA313IDBVR | IC OPAMP GP 1 CIRCUIT SOT23-5 | U3, U4, U5, U6 | 4 | Texas Instruments | OPA313IDBVR | Volume Production | Digi-Key | 296-35607-1-ND | 1.15 | 4.59
 | 5V0_3V3_LDO | IC REG LINEAR 3.3V 1A DPAK | VR1 | 1 | ON Semiconductor | NCP1117DT33T5G | Volume Production | Digi-Key | NCP1117DT33T5GOSCT-ND | 0.61296 | 0.61296
 | CRYSTAL_25MHZ | CRYSTAL 25.0000MHZ 12PF SMD | Y1 | 1 | Kyocera AVX | CX2520DB25000H0FLJC1 | Volume Production | Digi-Key | 1253-1724-1-ND | 0.939 | 0.939

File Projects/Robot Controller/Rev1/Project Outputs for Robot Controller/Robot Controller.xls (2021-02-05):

DesignItemId | Line # | Description | Designator | Quantity | Manufacturer 1 | Manufacturer Part Number 1 | Supplier 1 | Supplier Part Number 1 | Supplier Stock 1 | Supplier Unit Price 1 | Supplier Subtotal 1
CAP_1uF_50V_0805 |  | CAP CER 1UF 50V X7R 0805 | C1, C3, C11, C14, C17, C18, C19, C20, C21, C22, C23, C24, C25, C26, C27, C28, C29, C30, C31, C32, C33, C34, C35, C36, C37, C38, C39, C40, C41, C42, C43, C44, C45, C46, C47, C48, C49, C50, C51, C52, C53, C54, C55 | 43 | Samsung | CL21B105KBFNNNG | Digi-Key | 1276-6470-1-ND | 1938446 | 0.049 | 2.45
CAP_0.1uF_50V_0805 |  | CAP CER 0.1UF 50V X7R 0805 | C4, C5, C6, C7, C9, C10, C16 | 7 | Murata | GCM21BR71H104KA37K | Digi-Key | 490-8049-1-ND | 4281215 | 0.18 | 1.26
CAP_4.7uF_16V_0805 |  | CAP CER 4.7UF 16V X5R 0805 | C8, C15 | 2 | Samsung | CL21A475KOFNNNE | Digi-Key | 1276-1065-1-ND | 698565 | 0.19 | 0.38
CAP_14pF_50V_0603 |  | CAP CER 14PF 50V C0G/NP0 0603 | C12, C13 | 2 | Samsung | CL10C140JB8NNNC | Digi-Key | 1276-2187-1-ND
DIO_SCHOTTKY_30V_800mA |  | DIODE SCHOTTKY 30V 800MA USC | D1, D47 | 2 | Toshiba | CUS08F30,H3F | Digi-Key | CUS08F30H3FCT-ND | 144921 | 0.33 | 0.66
TVS_DIODE_UNIDIR_5V |  | TVS DIODE 5V 9.2V SMB | D2 | 1 | Bourns | SMBJ5.0A | Digi-Key | SMBJ5.0ABCT-ND | 11459 | 0.41 | 0.41
LED_GREEN |  | LED GREEN DIFFUSED 0805 SMD | D3 | 1 | Osram Opto | LGR971-KN-1 | Digi-Key | 475-1410-1-ND | 77846 | 0.27 | 0.27
LED_RGB |  | LED RGB DIFFUSED 4PLCC SMD | D4 | 1 | Broadcom Avago | ASMB-MTB1-0A3A2 | Digi-Key | 516-3280-1-ND | 160022 | 0.6 | 0.6
TVS_DIODE_UNIDIR_3.3V |  | TVS DIODE 3.3V 14.1V SOD523 | D5, D8, D9, D10, D11, D12, D13, D14, D15, D16, D17, D18, D19, D20, D21, D22, D23, D24, D25, D26, D27, D28, D29, D30, D31, D32, D33, D34, D35, D36, D37, D38, D39, D40, D41, D42, D43, D44, D45, D46 | 40 | ON Semiconductor | ESD5Z3.3T1G | Digi-Key | ESD5Z3.3T1GOSCT-ND | 30702 | 0.154 | 6.16
LED_YELLOW |  | LED YELLOW DIFFUSED 0805 SMD | D6 | 1 | Osram Opto | LYR976-PS-36 | Digi-Key | 475-2560-1-ND | 38199 | 0.28 | 0.28
TVS_DIODE_USB_5.5V |  | TVS DIODE 5.5V 8V SOT23-3 | D7 | 1 | Texas Instruments | TPD2E009DBZR | Digi-Key | 296-24657-1-ND | 18533 | 0.62 | 0.62
FUSE_1.25A_1206 |  | FUSE BOARD MOUNT 1.25A 63VAC/VDC 1206 | F1 | 1 | Littelfuse | 04661.25NRHF | Digi-Key | F11418CT-ND | 9787 | 0.81 | 0.81
2_AXIS_JOYSTICK_SMALL |  | JOYSTICK 10K OHM 2 AXIS TH | J1 | 1 | Adafruit Industries | 2765 | Digi-Key | 1528-1730-ND | 17 | 2.5 | 2.5
CON_PROGRAMMING |  | CONN HEADER SMD 10POS 1.27MM | J2 | 1 | Samtec | FTSH-105-01-F-DV-K | Digi-Key | SAM8796-ND | 7616 | 2.9 | 2.9
CMP-1502-03253-1 |  | Micro USB 2.0 Type B Receptacle WR-COM, Horizontal, SMT, with Pads and Pegs | J3 | 1 | Wurth Electronics | 629105136821 | Digi-Key | 732-3155-6-ND | 5836 | 1.21 | 1.21
2_AXIS_JOYSTICK |  | JOYSTICK 10K OHM 2 AXIS TH | J5, J6, J7, J8, J9 | 5 | SparkFun | 9032 | Digi-Key | 1568-1526-ND | 810 | 3.95 | 19.75
CONN_TERMINAL_2 |  | Header, 2-Pin | P1 | 1 | On-Shore Technology | OSTYK51102030 | Digi-Key | ED2953-ND | 28 | 1 | 1
RES_240Ω_0805_1% |  | RES 240 OHM 1% 1/8W 0805 | R1 | 1 | Vishay | CRCW0805240RFKEA | Digi-Key | 541-240CCT-ND | 25938 | 0.1 | 0.1
RES_20Ω_0805_1% |  | RES 20 OHM 1% 1/8W 0805 | R2, R4, R9, R10 | 4 | Yageo | RC0805FR-0720RL | Digi-Key | 311-20.0CRCT-ND | 376082 | 0.036 | 0.36
RES_100Ω_0805_1% |  | RES 100 OHM 1% 1/8W 0805 | R3 | 1 | Vishay Dale | CRCW0805100RFKEA | Digi-Key | 541-100CCT-ND | 244038 | 0.1 | 0.1
RES_10kΩ_0805_5% |  | RES 10K OHM 5% 1/8W 0805 | R5, R6, R7, R11, R12, R13, R14, R15, R16, R17, R18, R19, R20, R21, R22, R23, R24, R25, R26, R27, R28, R29, R30, R31, R32, R33, R34, R35, R36, R37, R38, R39, R40, R41, R42, R43, R44, R45, R46, R47, R48, R49, R50, R51, R52, R53, R54, R55, R56, R57, R58, R59, R60, R61, R62, R63, R64, R65, R66, R67, R68, R69, R70, R71, R72, R73, R74 | 67 | Panasonic | ERJ-6GEYJ103V | Digi-Key | P10KACT-ND | 782184 | 0.0201 | 2.01
RES_1kΩ_0805_1% |  | RES 1K OHM 1% 1/8W 0805 | R8 | 1 | Yageo | RC0805FR-071KL | Digi-Key | 311-1.00KCRCT-ND | 14060857 | 0.1 | 0.1
SW_MOMENTARY_PUSHBUTTON |  | TACTILE MOMENTARY PUSHBUTTON SPST | S1, S2, S3, S4, S5, S6, S7, S8, S9, S10, S11, S12, S13, S14, S15, S16 | 16 | SparkFun | COM-10302 | Digi-Key | 1568-1332-ND | 76 | 5.85 | 93.6
SW_SPDT |  | SWITCH TOGGLE SPDT 5A 120V | S17 | 1 | E-Switch | 100SP1T1B4M2QE | Digi-Key | EG2355-ND | 13060 | 1.92 | 1.92
SW_SPDT |  | SWITCH TOGGLE SPDT 5A 120V | S18 | 1 | E-Switch | 100SP1T1B4M2QE | Digi-Key | EG2355-ND | 13060 | 1.92 | 1.92
SW_TACTILE |  | SWITCH TACTILE SPST-NO 0.05A 12V | S19 | 1 | Omron | B3U-1000P | Digi-Key | SW1020CT-ND | 74875 | 0.92 | 0.92
TESTPOINT_LOOP |  | TESTPOINT THRUHOLE | TP1, TP2, TP3, TP4, TP5, TP6 | 6 | Keystone Electronics | 5002 | Digi-Key | 36-5002-ND | 641636 | 0.4 | 2.4
LDO_3.3V_600mA |  | IC REG LINEAR 3.3V 600MA SOT25 | U1 | 1 | Diodes | AP2112K-3.3TRG1 | Digi-Key | AP2112K-3.3TRG1DICT-ND | 939 | 0.49 | 0.49
MCU_STM32F446RET6 |  | ARM Cortex-M4 32-bit MCU+FPU, 512 KB Flash, 128 KB Internal RAM, 50 I/Os, 64-Pin LQFP, -40 to 85 degC, Tray | U2 | 1 | STMicroelectronics | STM32F446RET6 | Digi-Key | 497-15376-ND
POT_10K_SLIDE |  | SLIDE POT 10K OHM 0.1W TOP 20MM | VR1, VR2 | 2 | Bourns | PTA2043-2015DPB103 | Digi-Key | PTA2043-2015DPB103-ND | 699 | 1.29 | 2.58
CRYSTAL_25MHZ |  | CRYSTAL 25.0000MHZ 12PF SMD | Y1 | 1 | Kyocera AVX | CX2520DB25000H0FLJC1 | Digi-Key | 1253-1724-1-ND | 665 | 0.65 | 0.65

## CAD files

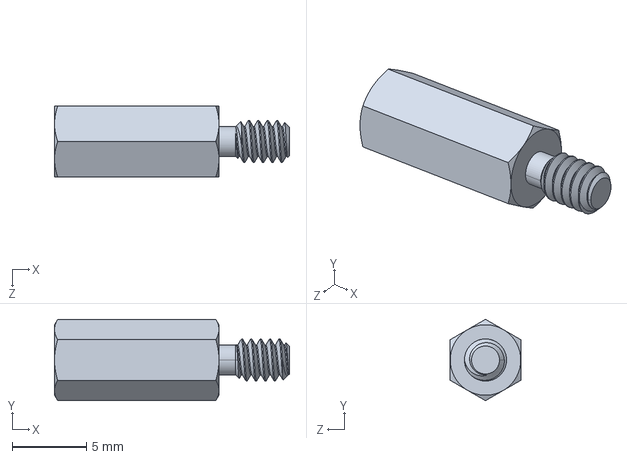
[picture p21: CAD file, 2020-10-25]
Projects/Gimbal/2021/Rev2/Board Shape/Standoff.STEP
15.9 x 5.50 x 4.76 mm

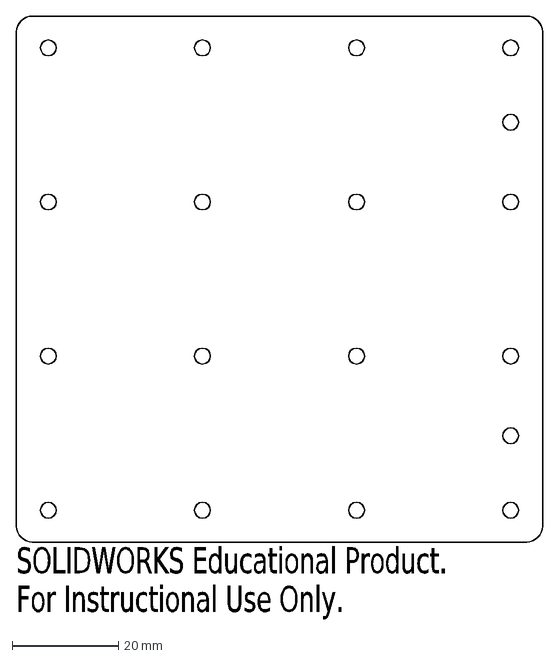
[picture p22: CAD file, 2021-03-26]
Projects/LED Matrix/Rev2/LED-PCB-Mock.DXF
SOLIDWORKS Educational Product.
For Instructional Use Only.

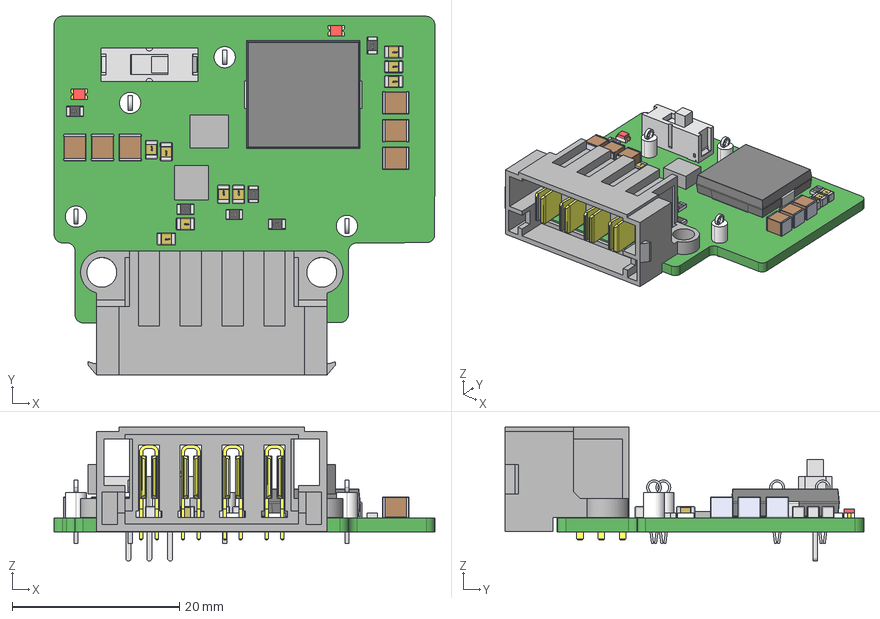
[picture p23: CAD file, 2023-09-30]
Projects/Power Distribution Board/Rev6.1/Power Distribution Board/Step Files/48V-5V Buck.step
45.5 x 42.9 x 16.0 mm
EG1218
Extruded x 2
0805_resistor x 6
red_led x 2
Open_CASCADE_STEP_translator_7.5_4.1.1
Lead x 2
MPT0401pins2
MPT04terminal2
GRT32EC81C476KE13L--3DModel-STEP-56544 x 6

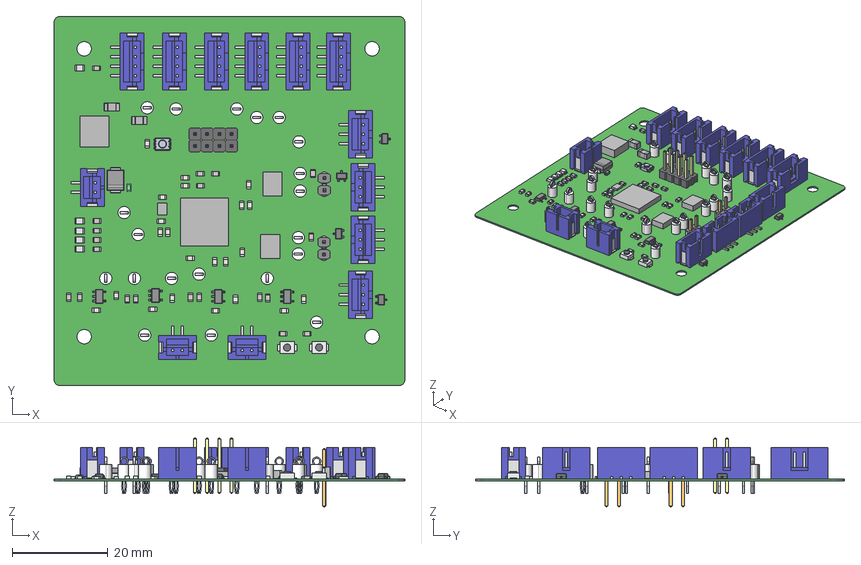
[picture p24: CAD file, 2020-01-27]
Projects/Safety/Rev1/assy/Safety-Rev1.step
73.2 x 77.0 x 14.4 mm
Extruded x 141
Open_CASCADE_STEP_translator_6.8_1.1.1 x 4
Leader x 12
B3B-PH-SM4-TB x 4
B4B-PH-SM4-TB x 6
User_Library-Header_Male_4Pin_PinArray x 2
User_Library-Header_Male_4Pin_BodyArray x 2
B2B-PH-SM4-TB x 3
User_Library-ptc06032-1
BODY_MF05A x 4
LEAD_MF05F x 20
b3u-1000p x 2
PTS830GM140GSMTRLFS
User_Library-DO-214AA_SMB
CircuitWorks-HDR1X2 x 2
model_RGB8421504 x 2

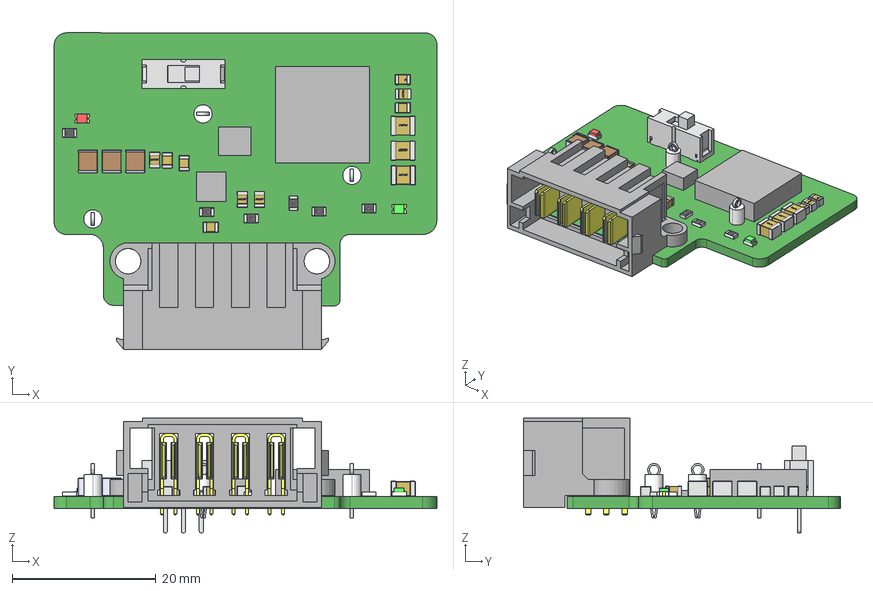
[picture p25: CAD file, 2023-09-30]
Projects/Power Distribution Board/Rev6.1/Power Distribution Board/Step Files/48-17V Buck Converter.step
53.3 x 44.1 x 16.0 mm
0805_resistor x 6
everlight-17-21-0805LED-GREEN
Extruded x 3
EG1218
red_led
MPT0401pins2
MPT04terminal2
GRT32EC81C476KE13L--3DModel-STEP-56544 x 3

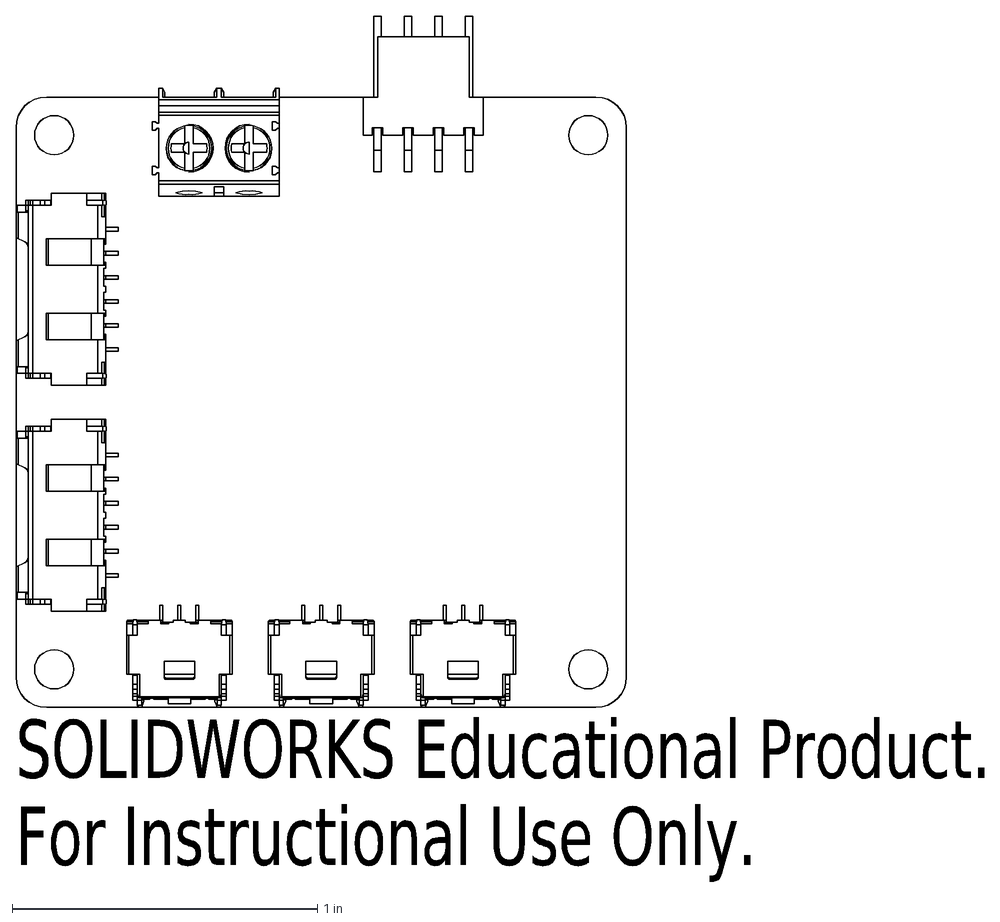
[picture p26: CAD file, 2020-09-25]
Projects/Gimbal/2021/Rev2/Board Shape/FrontConnectors.DXF
SOLIDWORKS Educational Product.
For Instructional Use Only.

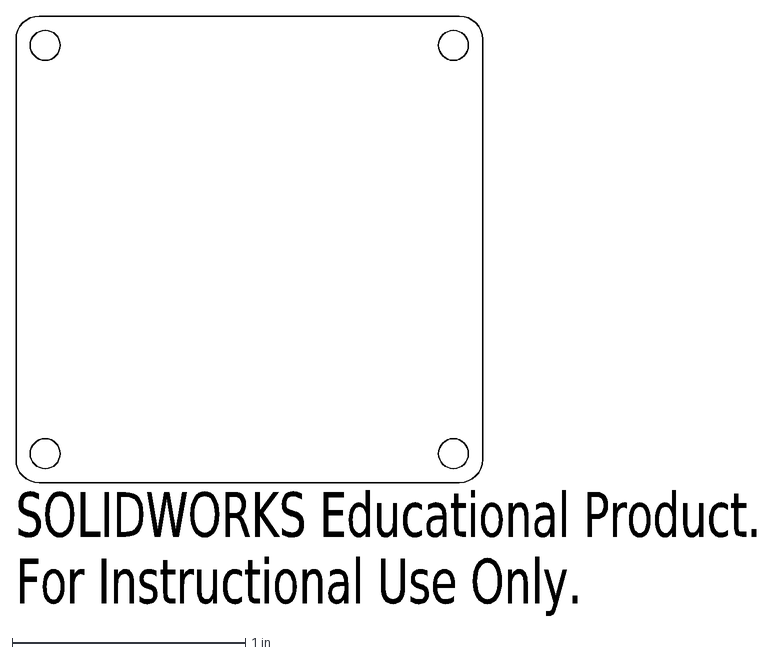
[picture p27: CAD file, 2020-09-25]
Projects/Gimbal/2021/Rev2/Board Shape/Shape.DXF
SOLIDWORKS Educational Product.
For Instructional Use Only.

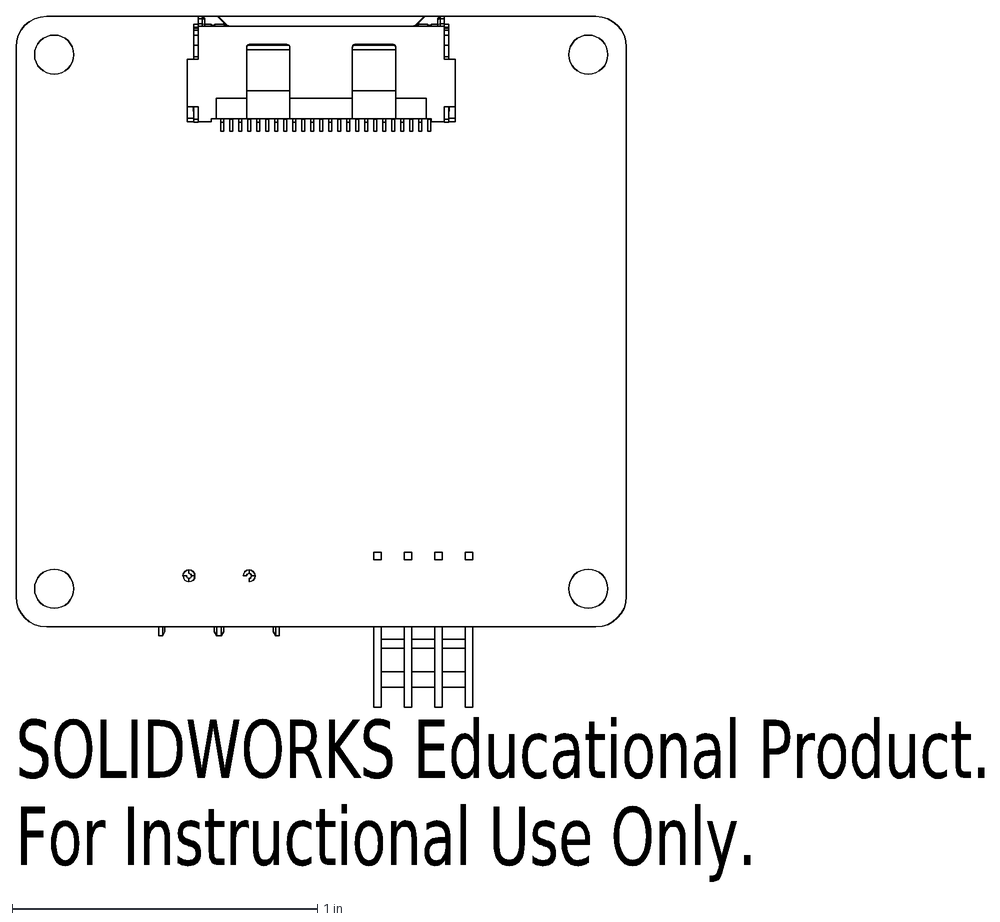
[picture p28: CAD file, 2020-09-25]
Projects/Gimbal/2021/Rev2/Board Shape/BackConnectors.DXF
SOLIDWORKS Educational Product.
For Instructional Use Only.

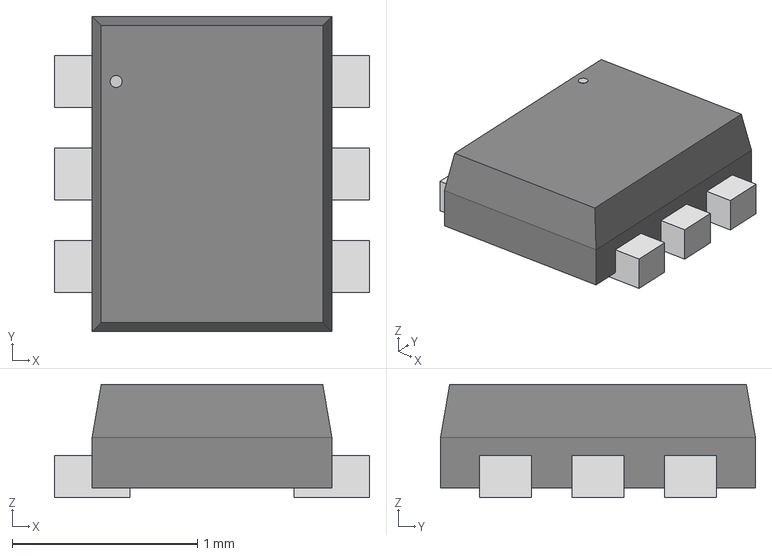
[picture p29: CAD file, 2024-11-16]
Projects/dd_current_sense/Rev1_vrmeredd/TPS564242DRLR_TEX.step
1.70 x 1.70 x 0.612 mm

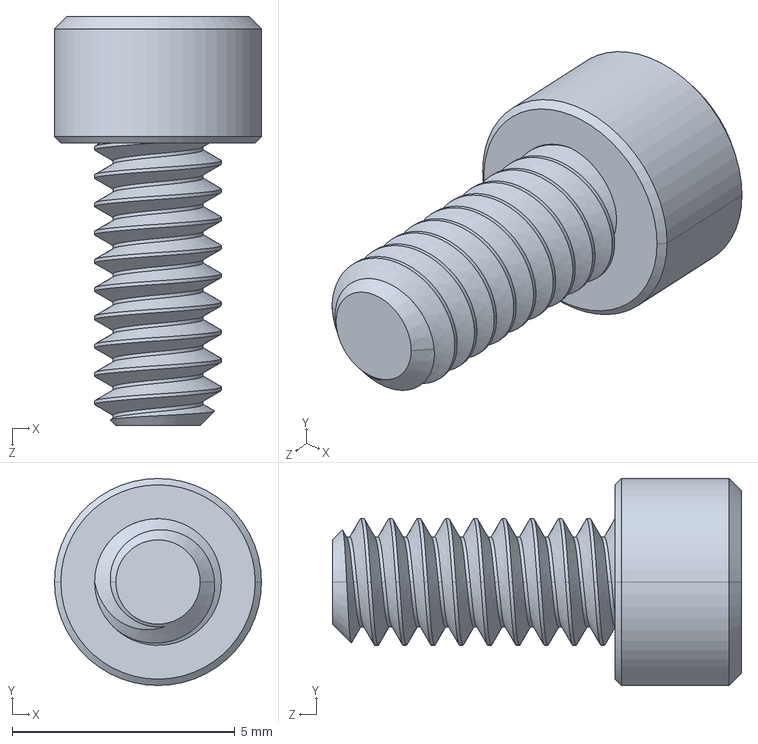
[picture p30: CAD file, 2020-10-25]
Projects/Gimbal/2021/Rev2/Board Shape/Screw.STEP
4.65 x 4.65 x 9.19 mm

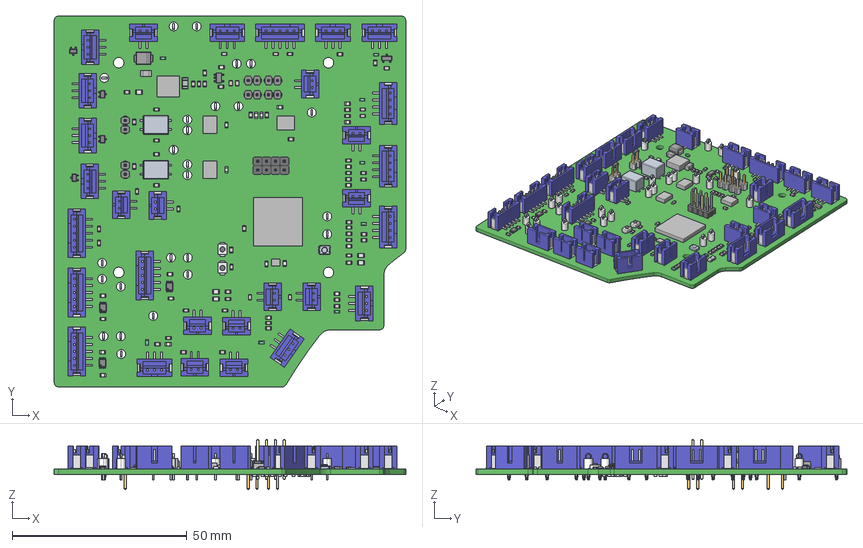
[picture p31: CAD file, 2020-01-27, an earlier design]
Projects/Arm/Rev1/Arm-PCB-Rev1.step
100.6 x 106.1 x 14.4 mm
Extruded x 307
B2B-PH-SM4-TB x 12
CircuitWorks-HDR1X2 x 6
User_Library-DO-214AA_SMB
BODY_MF05A
LEAD_MF05F x 5
DCU0008A x 3
B3B-PH-SM4-TB x 10
B5B-PH-SM4-TB x 5
b3u-1000p x 2
PTS830GM140GSMTRLFS
User_Library-3-lead_sot23-3
User_Library-ptc06032-1 x 8
B4B-PH-SM4-TB x 3
User_Library-Header_Male_4Pin_PinArray x 2
User_Library-Header_Male_4Pin_BodyArray x 2
Open_CASCADE_STEP_translator_6.8_1.1.1 x 4
Leader x 12
dr331 x 2
model_RGB8421504 x 2

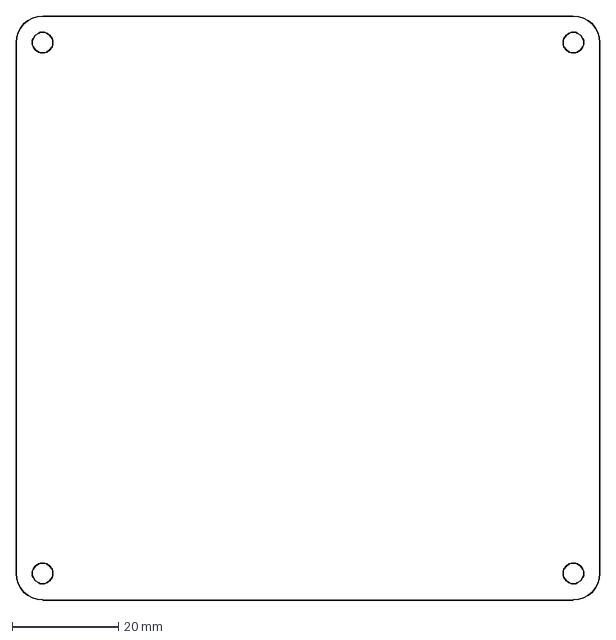
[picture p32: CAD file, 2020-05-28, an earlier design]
Projects/Battery Management System/Rev1/BMS Board Outline.dxf
110.0 x 110.0 mm

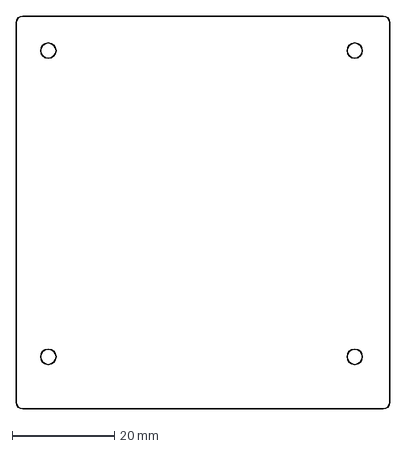
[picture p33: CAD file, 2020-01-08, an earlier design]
Projects/Gimbal/2021/Rev1/GimbalorSafety.dxf
73.2 x 77.0 mm

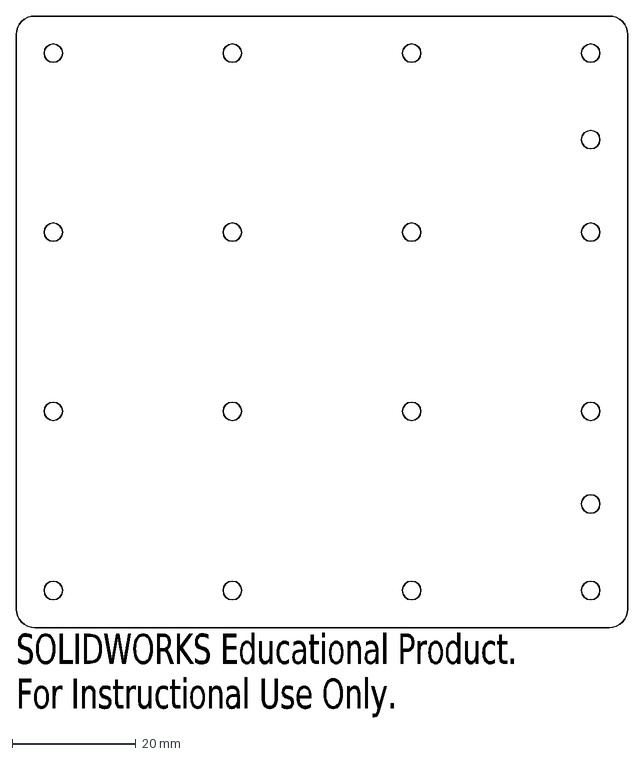
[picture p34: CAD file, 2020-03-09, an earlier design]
Projects/LED Matrix/Rev1/LED-PCB-Mock.DXF
SOLIDWORKS Educational Product.
For Instructional Use Only.

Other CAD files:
Projects/Gimbal/2021/Rev1/assy/Gimbal-PCB-Rev1.step
Projects/Science/Rev1/MR20-SC-PCB-NA.DXF
Projects/Battery Management System/Rev1/BMS Board Outline.dwg

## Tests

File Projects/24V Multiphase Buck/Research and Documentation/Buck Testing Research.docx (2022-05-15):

# Buck Testing

# Unpowered Tests

- 10K on EN pins is actually 8.7k – IDK, don’t trust this multimeter

# Performance Tests

## Line Regulation

Line regulation is the ability of a power supply to maintain and constant output voltage, despite changes in the input voltage.

Note: should probably use a more accurate/sensitive voltmeter for this test since line regulation is expected to be <0.1%.

Line Regulation(∆V0)/(∆Vi)∙100%

Vi | Vo
25 | 0
30 | 23.76
32 | 23.75
34 | 23.75
36 | 23.75
38 | 23.75
40 | 23.76
42 | 23.76
44 | 23.76
46 | 23.76
48 | 23.76
50 | 23.78
52 | 23.82

Line Regulation= 0.07/22∙100%=0.318%

Given that the actual operating voltage is 40.8 – 50.2V, the line regulation across that interval would be,

Line Regulation= 0.02/9.4∙100%=0.213%

d

## Load Regulation

Load regulation is the capability to maintain a constant voltage level at the output despite changes in the supply’s load.

Load Regulation= (Vno load-Vfull load)/(Vfull load)

Where,

- Vmin-load is the voltage when the output is open circuit
- Vmax-load is the maximum expected/allowable load
- Vnom-load is the voltage at a typical or specified load

## Efficiency

Efficiency is who effectively the buck steps down the voltage, how much power is lost.

Efficiency= (Pout)/(Pin)∙100%

Considerations for multiphase:

- PCB impedances cause voltage drops along the output trace of each phase as it routes from the switching node pins of the IC to the load
- A good, symmetric layout will minimize this impact. Layout asymmetries, however, can lead to imbalances in the outputs of the buck
- In order to properly calculate the efficiency of a multiphase buck, need to measure the current and voltage output at each phase individually.

## Output Ripple

Output ripple is the variation in voltage at the output caused by the switching nature of the regulator.

# Questions for Farris

- Better multimeter/voltmeter?
- How to test load regulation and efficiency?

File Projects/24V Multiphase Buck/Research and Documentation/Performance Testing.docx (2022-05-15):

# Buck Testing

# Unpowered Tests

- 10K on EN pins is actually 8.7k – IDK, don’t trust this multimeter

# Performance Tests

## Line Regulation

Line regulation is the ability of a power supply to maintain and constant output voltage, despite changes in the input voltage.

Note: should probably use a more accurate/sensitive voltmeter for this test since line regulation is expected to be <0.1%.

Line Regulation(∆V0)/(∇Vi)∙100%

Vi | Vo
25 | 0
30 | 23.76
32 | 23.75
34 | 23.75
36 | 23.75
38 | 23.75
40 | 23.76
42 | 23.76
44 | 23.76
46 | 23.76
48 | 23.76
50 | 23.78
52 | 23.82

Line Regulation= 0.07/22∙100%=0.318%

Given that the actual operating voltage is 40.8 – 50.2V, the line regulation across that interval would be,

Line Regulation= 0.02/9.4∙100%=0.213%

d

## Load Regulation

Load regulation is the capability to maintain a constant voltage level at the output despite changes in the supply’s load.

Load Redulation= (Vmin-load-Vmax-load)/(Vnom-load)

Where,

- Vmin-load is the voltage when the output is open circuit
- Vmax-load is the maximum expected/allowable load
- Vnom-load is the voltage at a typical or specified load

## Efficiency

Efficiency is who effectively the buck steps down the voltage, how much power is lost.

Efficiency= (Pout)/(Pin)∙100%

Considerations for multiphase:

- PCB impedances cause voltage drops along the output trace of each phase as it routes from the switching node pins of the IC to the load
- A good, symmetric layout will minimize this impact. Layout asymmetries, however, can lead to imbalances in the outputs of the buck
- In order to properly calculate the efficiency of a multiphase buck, need to measure the current and voltage output at each phase individually.

## Output Ripple

Output ripple is the variation in voltage at the output caused by the switching nature of the regulator.

Can measure it peak to peak.

Can reduce output ripple by adding:

- More output capacitance
- LC filters
- Common Mode Chokes

## Transient Response

Load transient response is the response characteristic to a sudden load fluctuation, that is, the time until the output voltage returns to a pre-set value after having fallen or risen, and the waveform of the output voltage.

Measuring the transient response requires applying or removing a load suddenly and observing the effect on the output voltage.

Transient equation:

(2∙∆I_0)/(f_(sw) ∙C_(OUT))

Based on this equation, the transient response can be improved by either increasing the output capacitance or increasing the switching frequency. Increasing the crossover frequency can also improve transient response.

## Measuring Significant Waveforms

Once we get some shots of each of the waveforms, can delve into what they should look like etc.

### SW1:

### SW2:

### HS1:

### HS2:

### LS1:

### LS2:

### FB1:

### FB2:

## Output Overcurrent Protection

Current limit is set to 15A per channel. To test this would need to apply a load of greater than 15A and see if it limits it and doesn’t explode. There are also two different current limit settings which are programmed via R18. The current limiting performance in each case should be compared.

### Latch off Current Limit

### Foldback Current Limit

## Output Overvoltage Protection

From datasheet: The output overvoltage-protection circuit protects the load under output overvoltage conditions. If the output voltage rises by more than 10% of its nominal value, the high-side MOSFET is turned off until the overvoltage condition clears.

If PWM mode is selected, the low-side MOSFET remains on until the output overvoltage condition clears. In this case, the current through the low-side MOSFET can reach a large value depending on the amount of overvoltage and output capacitance. If DCM is selected, the low-side MOSFET is turned off whenever the inductor current reaches zero. In this mode, the low-side MOSFET is turned on every 10 clock cycles to refresh the BST_ capacitor.

- How to test load regulation and efficiency?
- What is the operating voltage range for the battery?
- Does testing the output overvoltage protection just mean applying too much voltage to the buck and see what happens at the output?

# Changes so Far

- Switched RT to 32200 ohm
- Removed R186

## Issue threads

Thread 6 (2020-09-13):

Reference Designators on CAN Breakout

aascalon, 2020-09-13:
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

Please revert the designators back to the default (e.g., D4, D5...). You can have the CAN1_RX stuff, just make it a text instead of refdes.

ChristopherA057, 2020-09-14:
I fixed the designators and replaced the connectors, could use a quick review before closing the issue

Closed 2020-11-08.

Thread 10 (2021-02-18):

[ARM] Missing CS Connection for AEAT-6012 Encoders

a-gratton, 2021-02-18:
The CS lines for the AEAT-6012 SPI buses are not connected on arm, however this encoder **requires** a falling CS edge to output data (it can't just be tied to ground even if there's only 1 slave on the bus). See page 4 of the [datasheet](https://docs.broadcom.com/doc/AV02-0188EN).

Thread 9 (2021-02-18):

[ARM] Connect SWO to Debug Header

a-gratton, 2021-02-18:
Currently SWO is not connected to the debug header, so firmware is unable to print over serial for debugging.

lwbantoto, 2021-08-04:
Is this referring to a specific board? @a-gratton

Below is our standard programming connector pinout.
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

a-gratton, 2021-08-04:
On the arm board the SWO pin wasn't actually connected in the layout

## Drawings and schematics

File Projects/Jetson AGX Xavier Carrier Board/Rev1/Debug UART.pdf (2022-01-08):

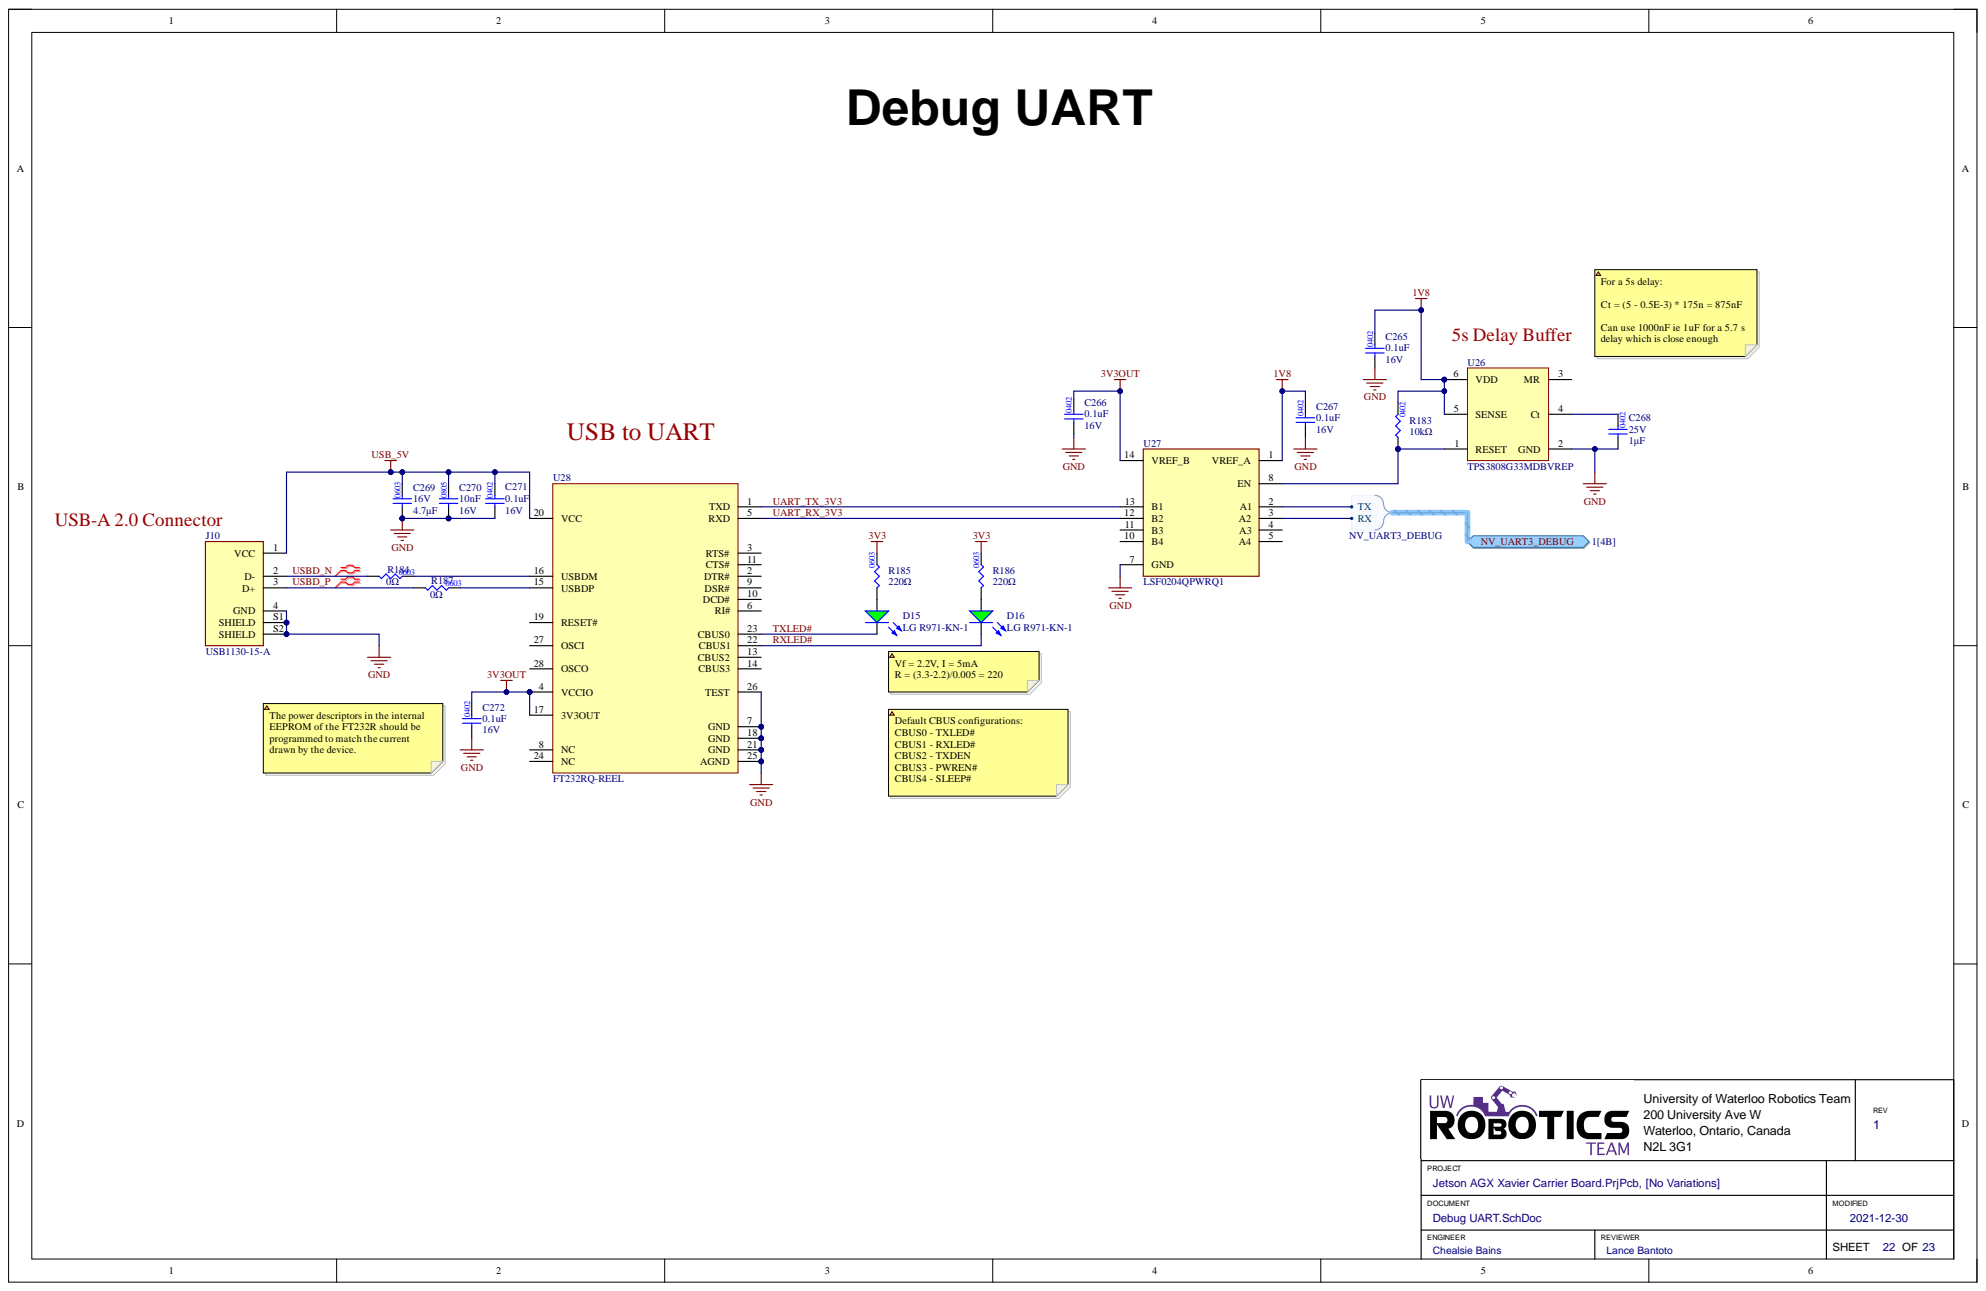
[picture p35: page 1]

Can
delay which is close enough

USBDM 16 | 1 1 3V3 3V3

The power descriptors in
EEPROM of
program
drawn by

Unive rsity of W ate rlo o Ro b otics T e a m 2 0 0 Unive rsity Ave W W ate rlo o, Onta rio, Ca n a d a N2 L 3G1 | R E V 1

P ROJ E CT Jetson A G X Xavier Car r ier Board. P r j Pcb, [ No Var iat ions]

DOC U M E N T Debug U A R T. SchDoc | MOD IFI E D 2021-12-30

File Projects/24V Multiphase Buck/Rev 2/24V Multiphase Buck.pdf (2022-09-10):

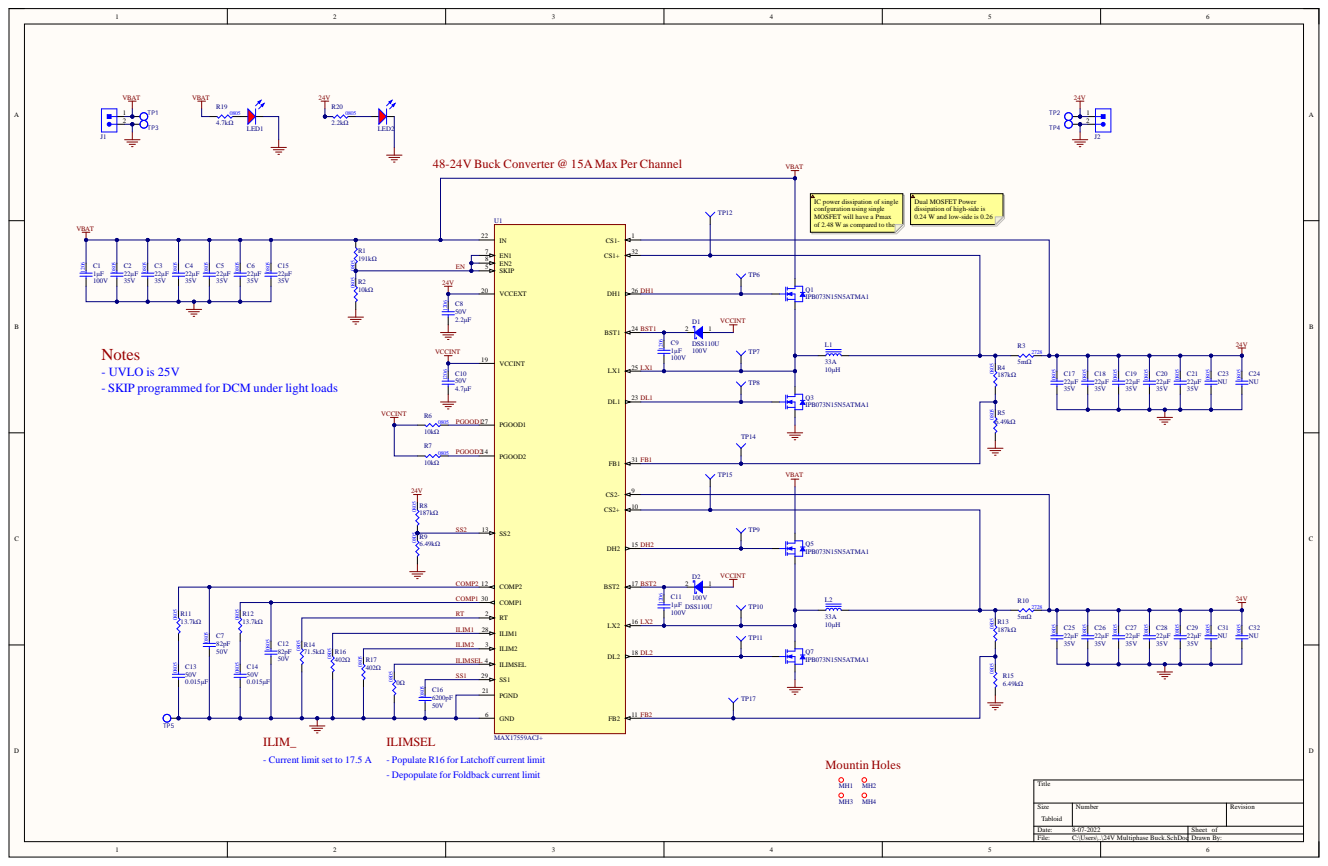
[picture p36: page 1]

IC power dissipation of single
confguration
MOSFET will
of 2.48 W as compared

Dual MOSFET Power
dissipation of
0.24 W and low-side is 0.26

COMP1 30

ILIM1 | | ILIM1 28

ent limit set to 17.5

Size Tabloid | Nu mber | Revision

Date: 8-07-2022 | Sheet of
File: C:\Users\. .\24V Multiphase Buck.SchDoc | Drawn By:

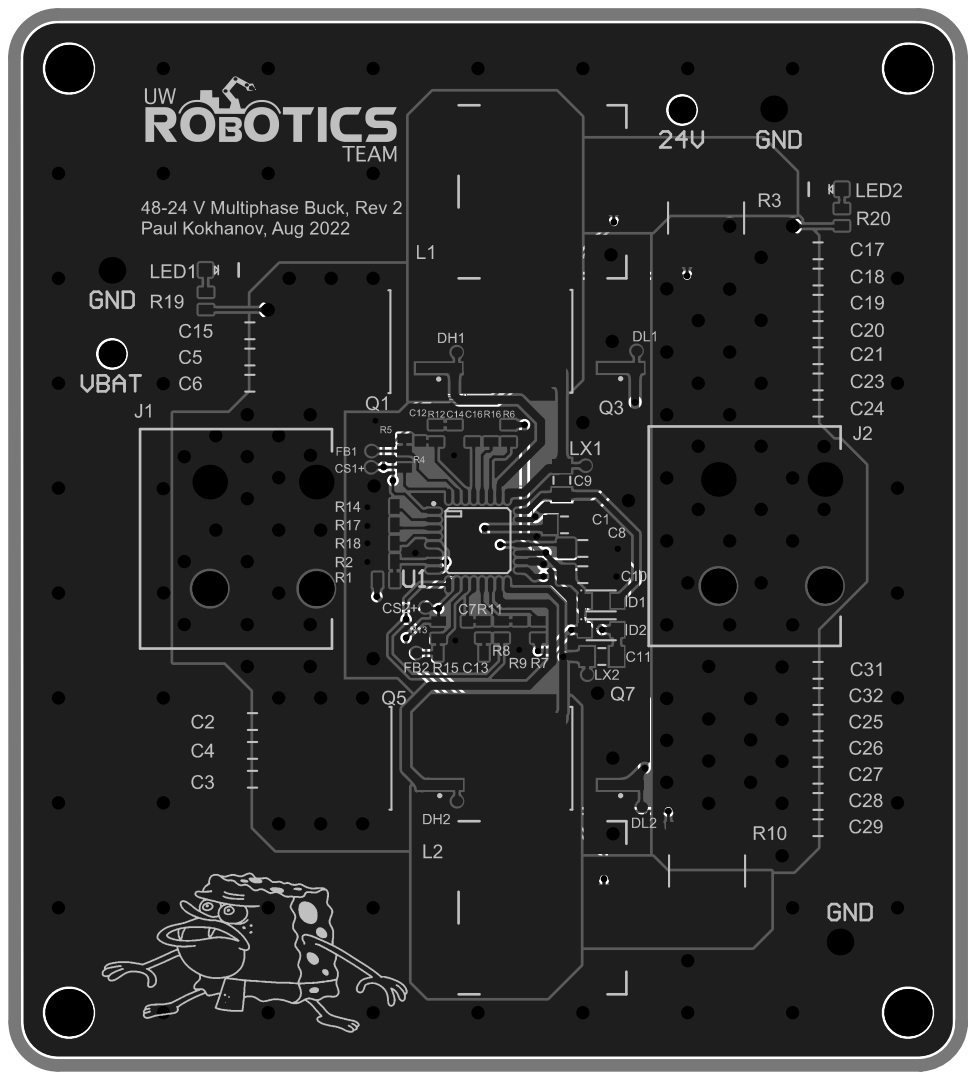
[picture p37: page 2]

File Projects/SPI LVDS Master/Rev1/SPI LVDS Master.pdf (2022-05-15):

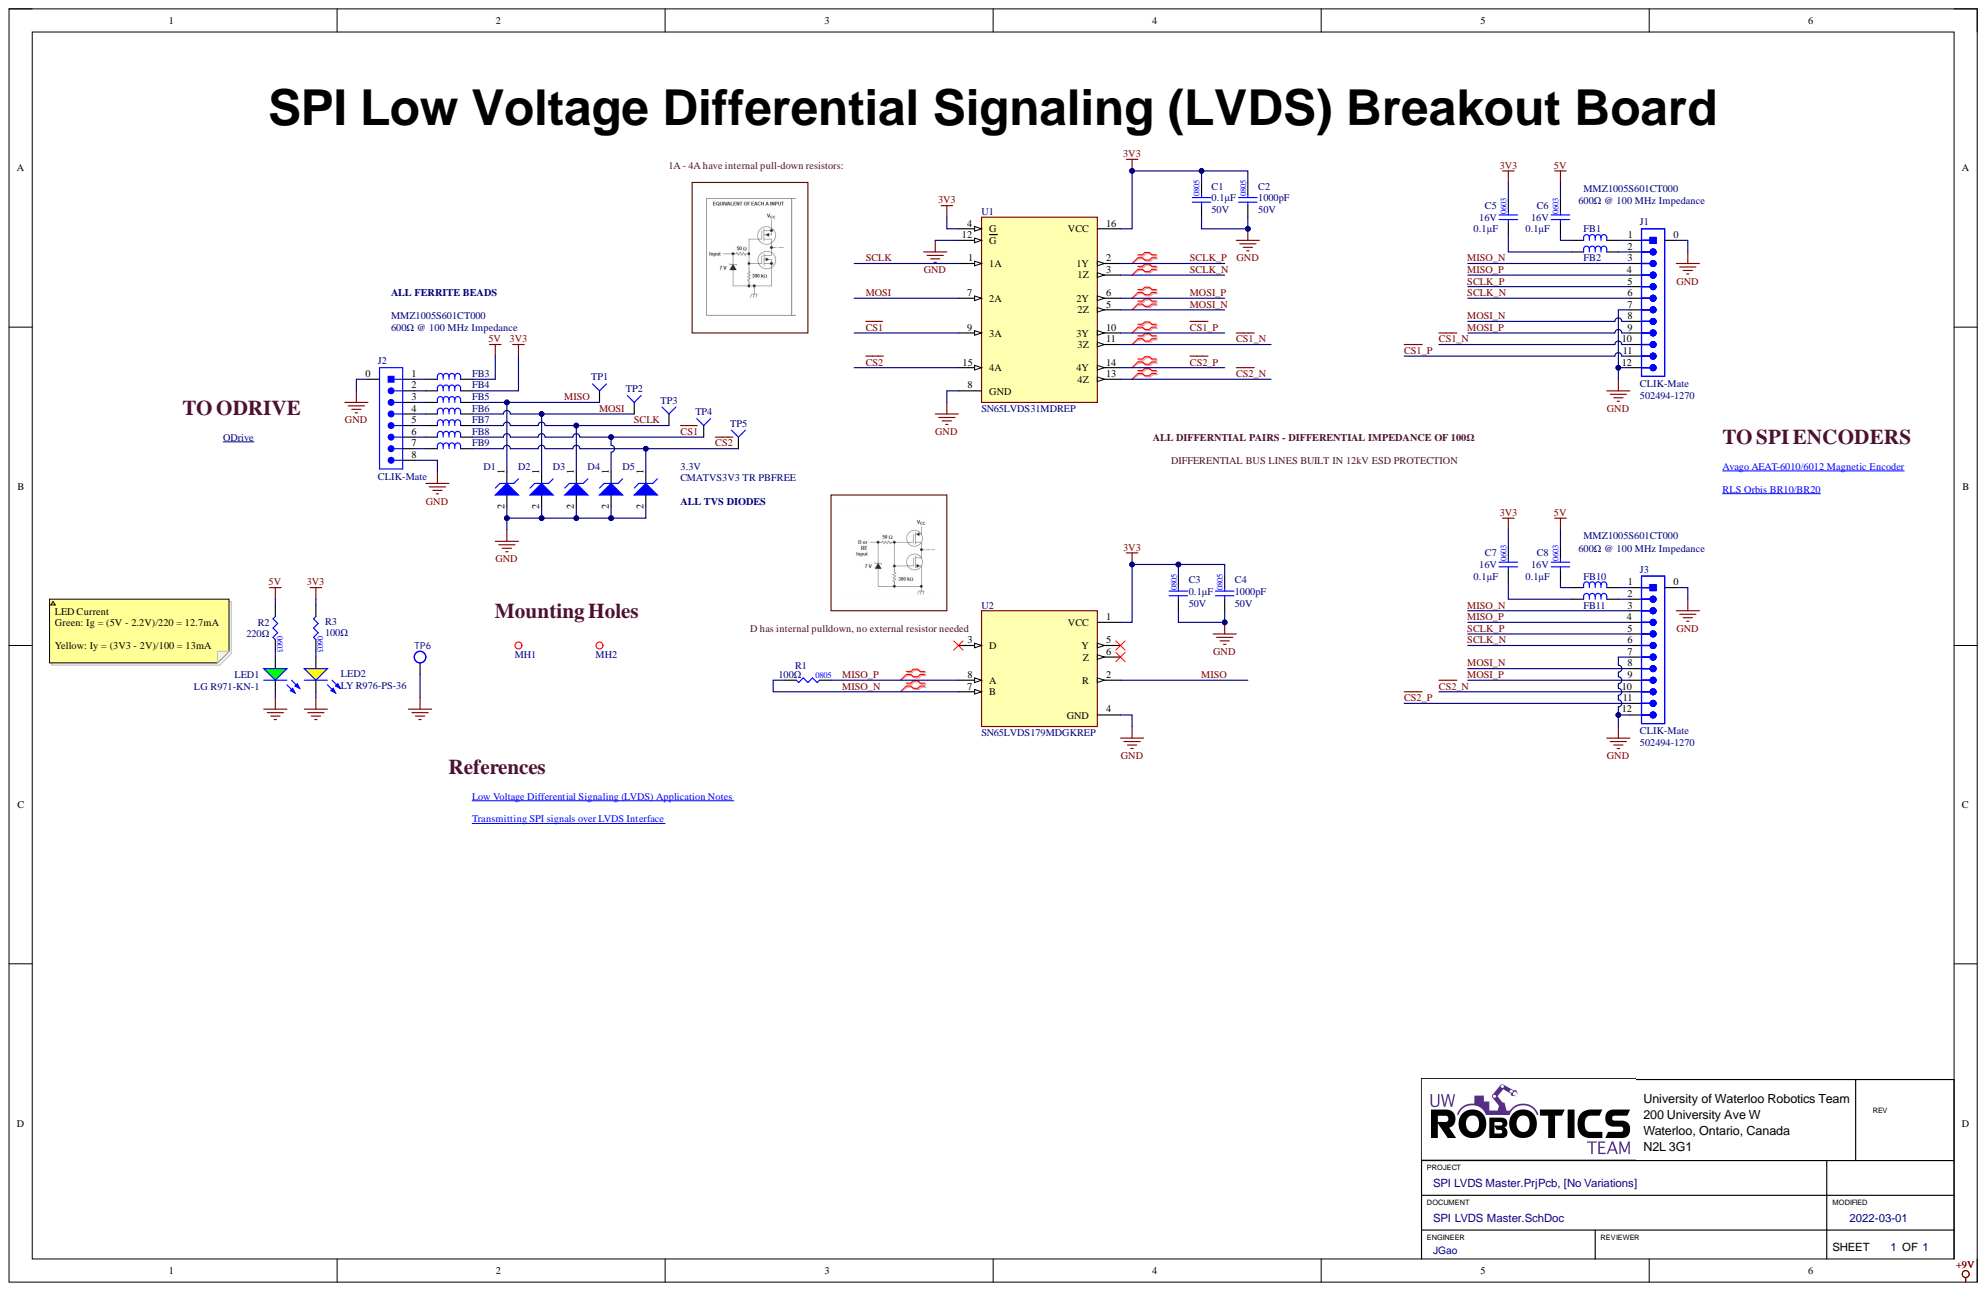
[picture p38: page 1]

SPI Low Voltage Differential Signaling (LVDS) Breakout Board ENGINEER

ternal pull-down resistors:

PAIRS - DIFFERENTIAL IMPEDANCE OF 100

DIFFERENTIAL BUS LINES BUILT IN 12kV ESD PROTECTION

Avago AEAT-6010/6012 Magnetic Encoder (https://www.mouser.ca/datasheet/2/678/av02_0188en-1855336.pdf)

tial Signaling (LVDS) Application Notes (https://www.ti.com/lit/an/slla014a/slla014a.pdf?ts=1641520445544)

ting SPI signals over

Unive rsity of W ate rlo o Ro b otics T e a m 2 0 0 Unive rsity Ave W W ate rlo o, Onta rio, Ca n a d a N2 L 3G1 | R E V

P ROJ E CT S P I LV D S Master . P r j Pcb, [ No Var iat ions]

DOC U M E N T S P I LV D S Master . SchDoc | MOD IFI E D 2022-03-01

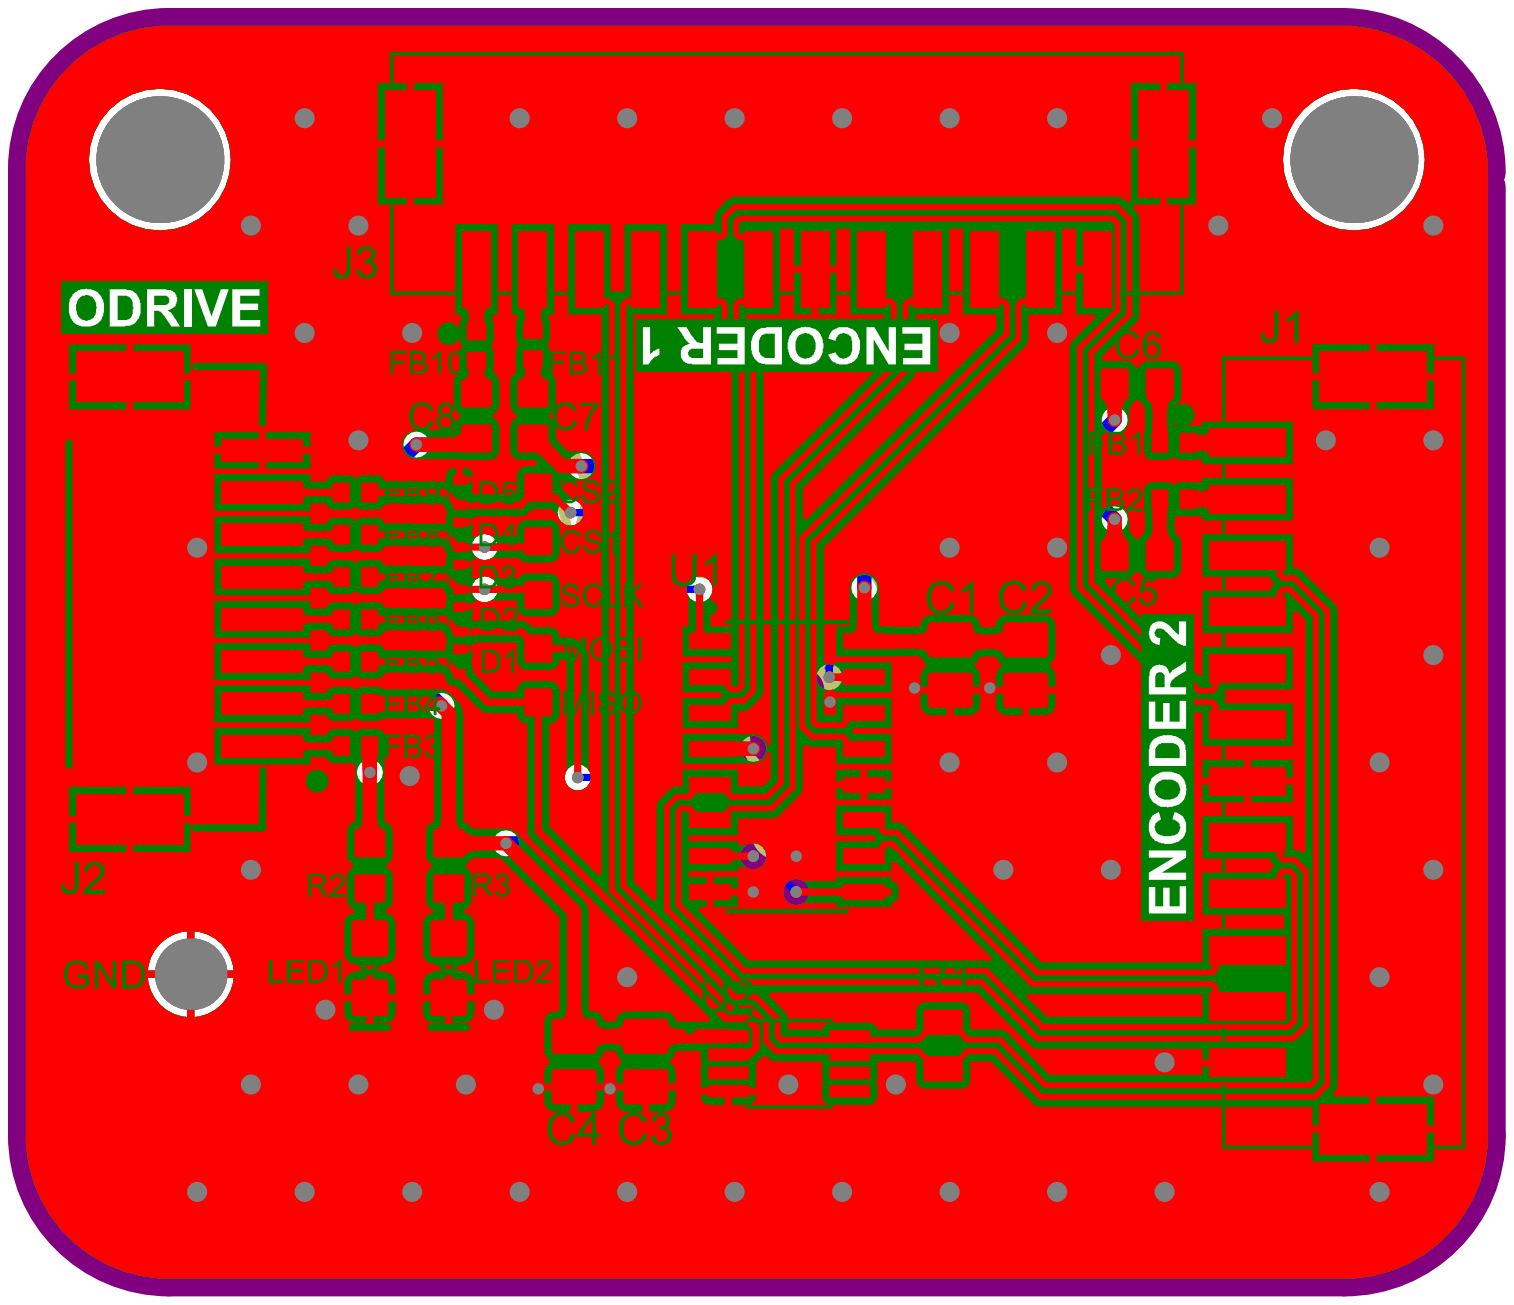
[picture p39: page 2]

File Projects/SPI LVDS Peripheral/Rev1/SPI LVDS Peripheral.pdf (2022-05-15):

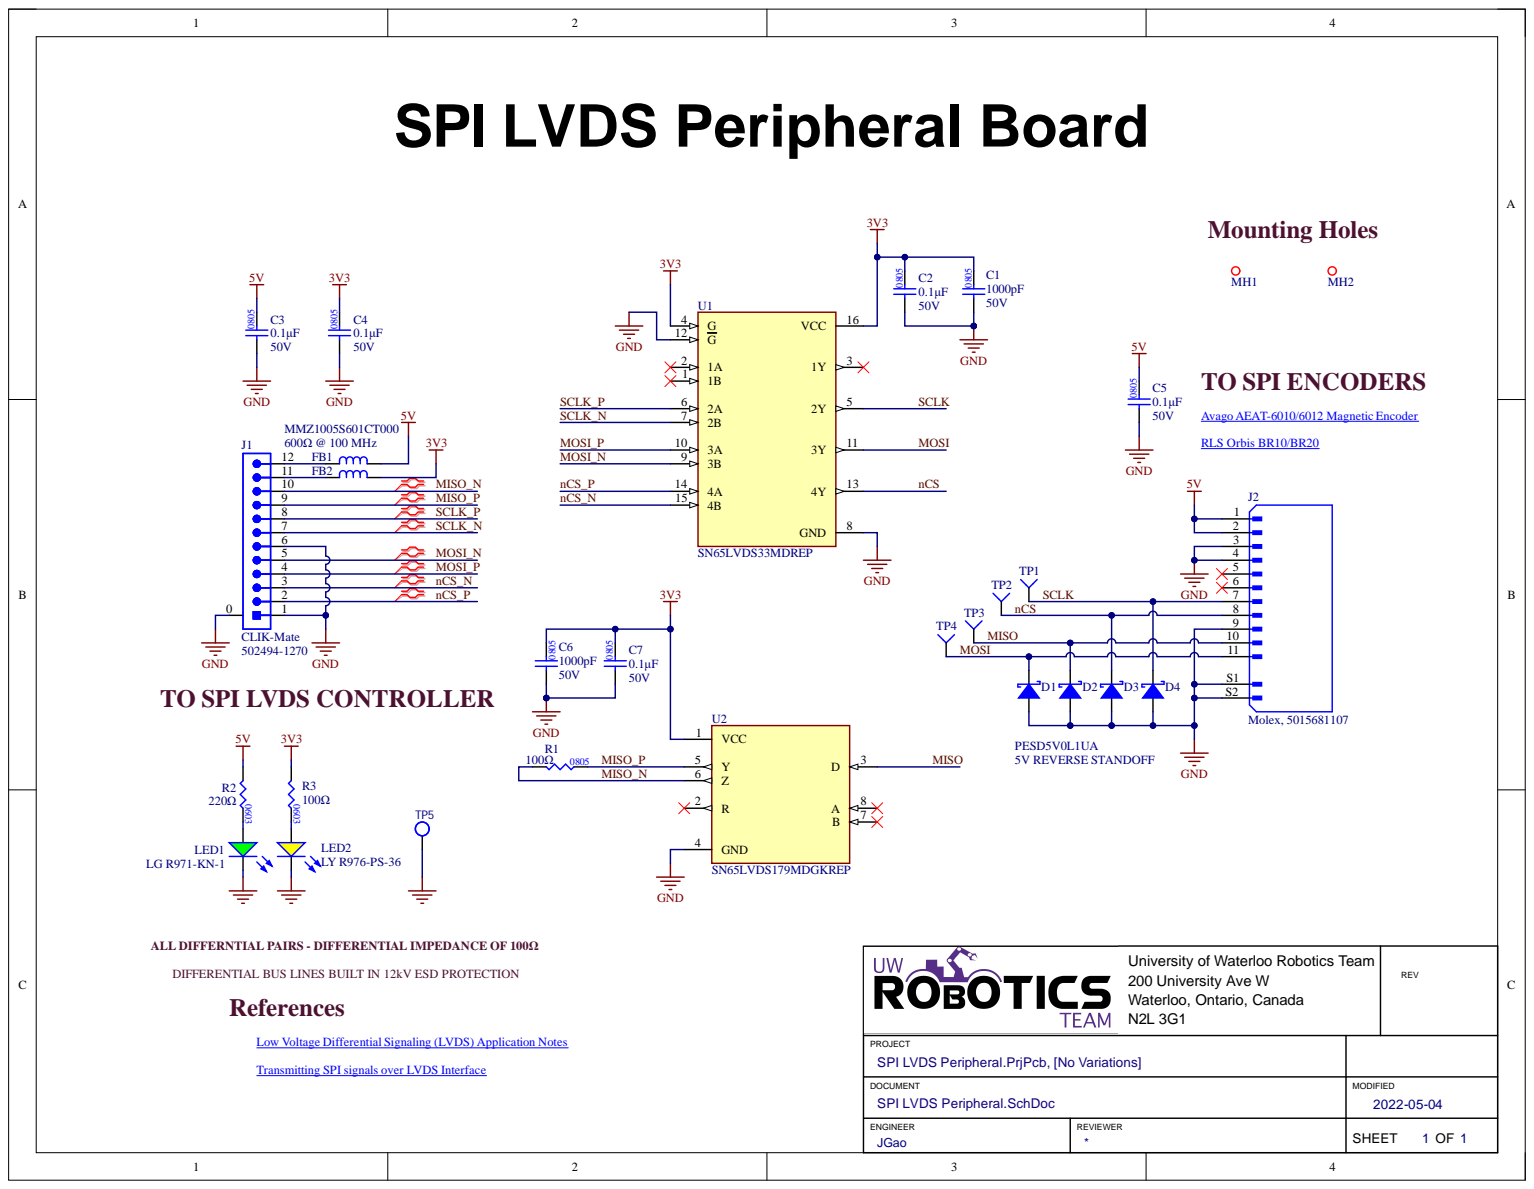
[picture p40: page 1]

SPI LVDS Peripheral Board

TO SPI ENCODERS Avago AEAT-6010/6012 Magnetic Encoder RLS Orbis BR10/BR20

Univer sit y of Waterloo Robotic s Team 200 Univer sit y Ave W Waterloo, Ontario, Canada N2L 3G1 | REV

PROJECT

DOCUMENT | 1 JGao SPI LVDS Peripheral.PrjPcb, [No Variations] SPI LVDS Peripheral.SchDoc MODIFIED 202 2 -0 5 -0 4

ENGINEER | REVIEWER * | SHE E T 1 OF

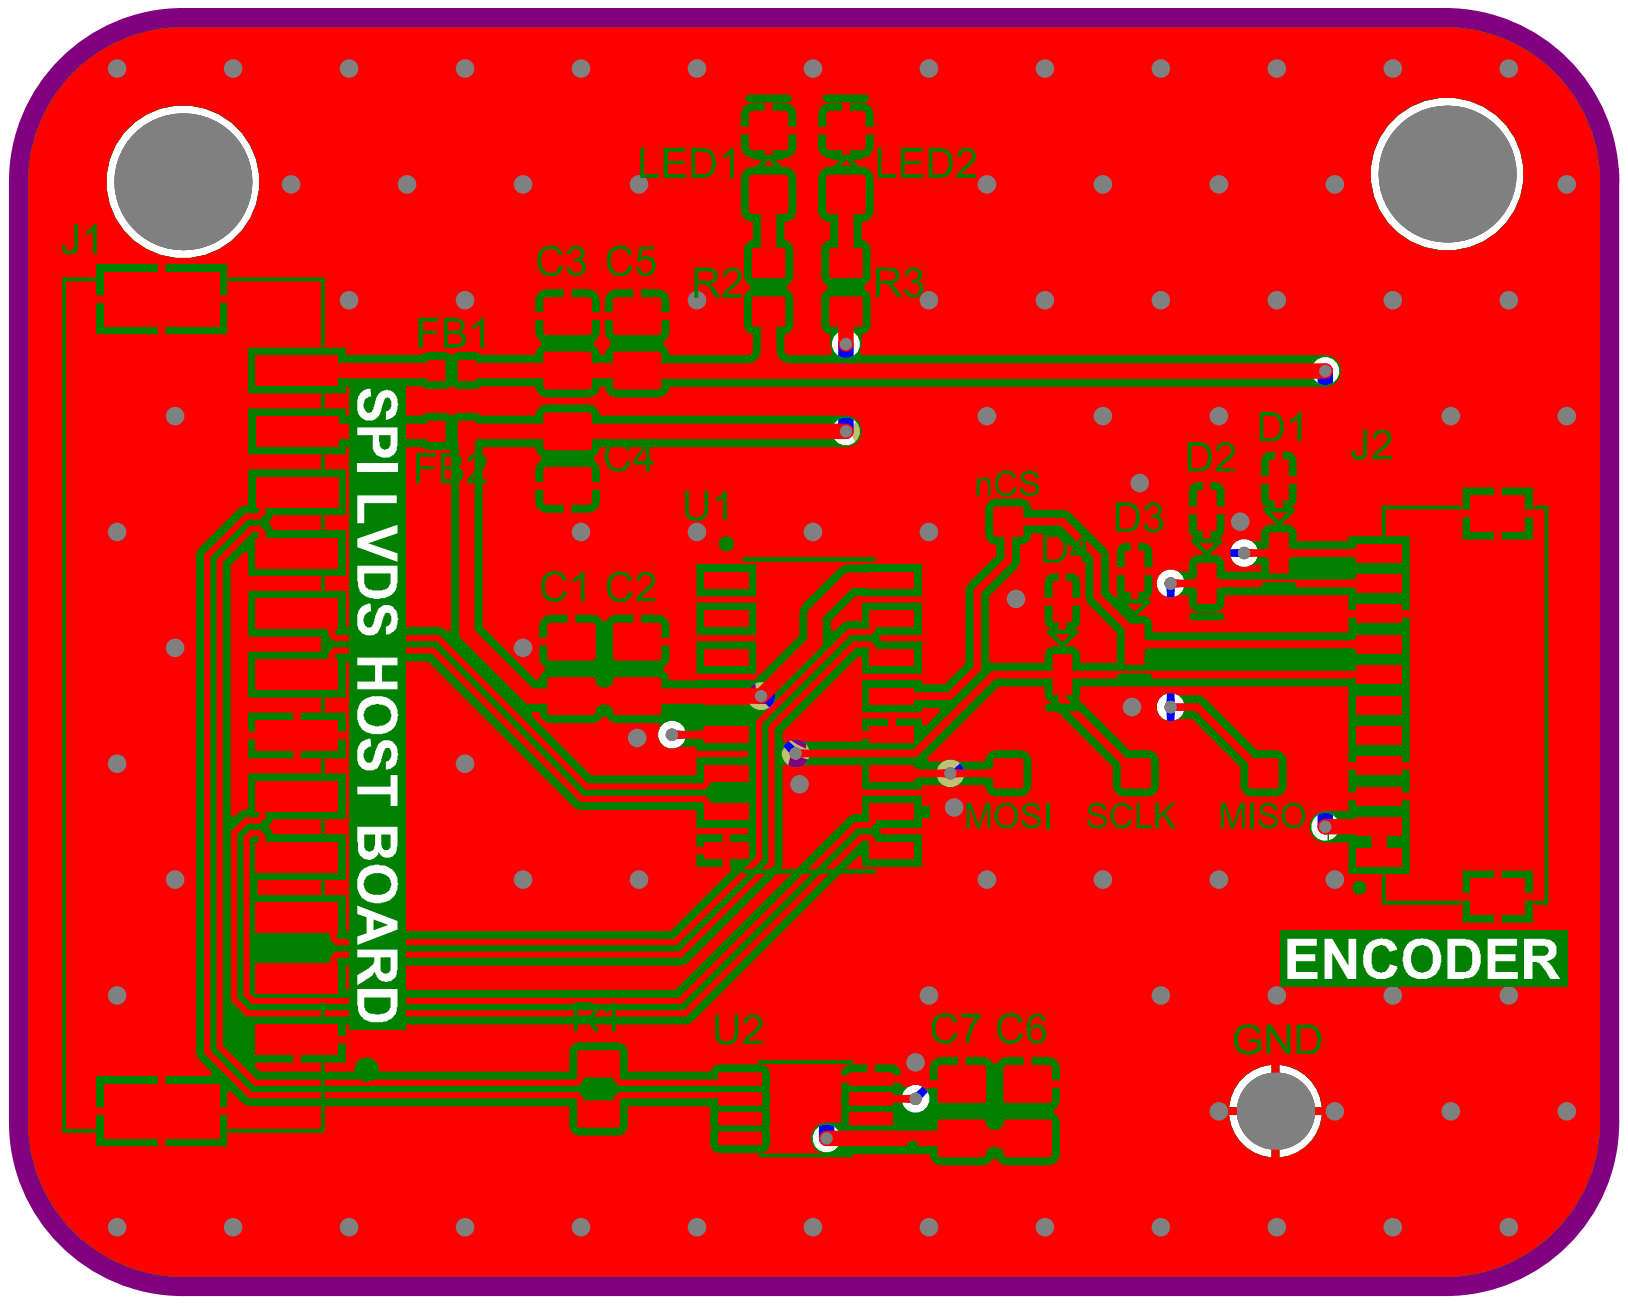
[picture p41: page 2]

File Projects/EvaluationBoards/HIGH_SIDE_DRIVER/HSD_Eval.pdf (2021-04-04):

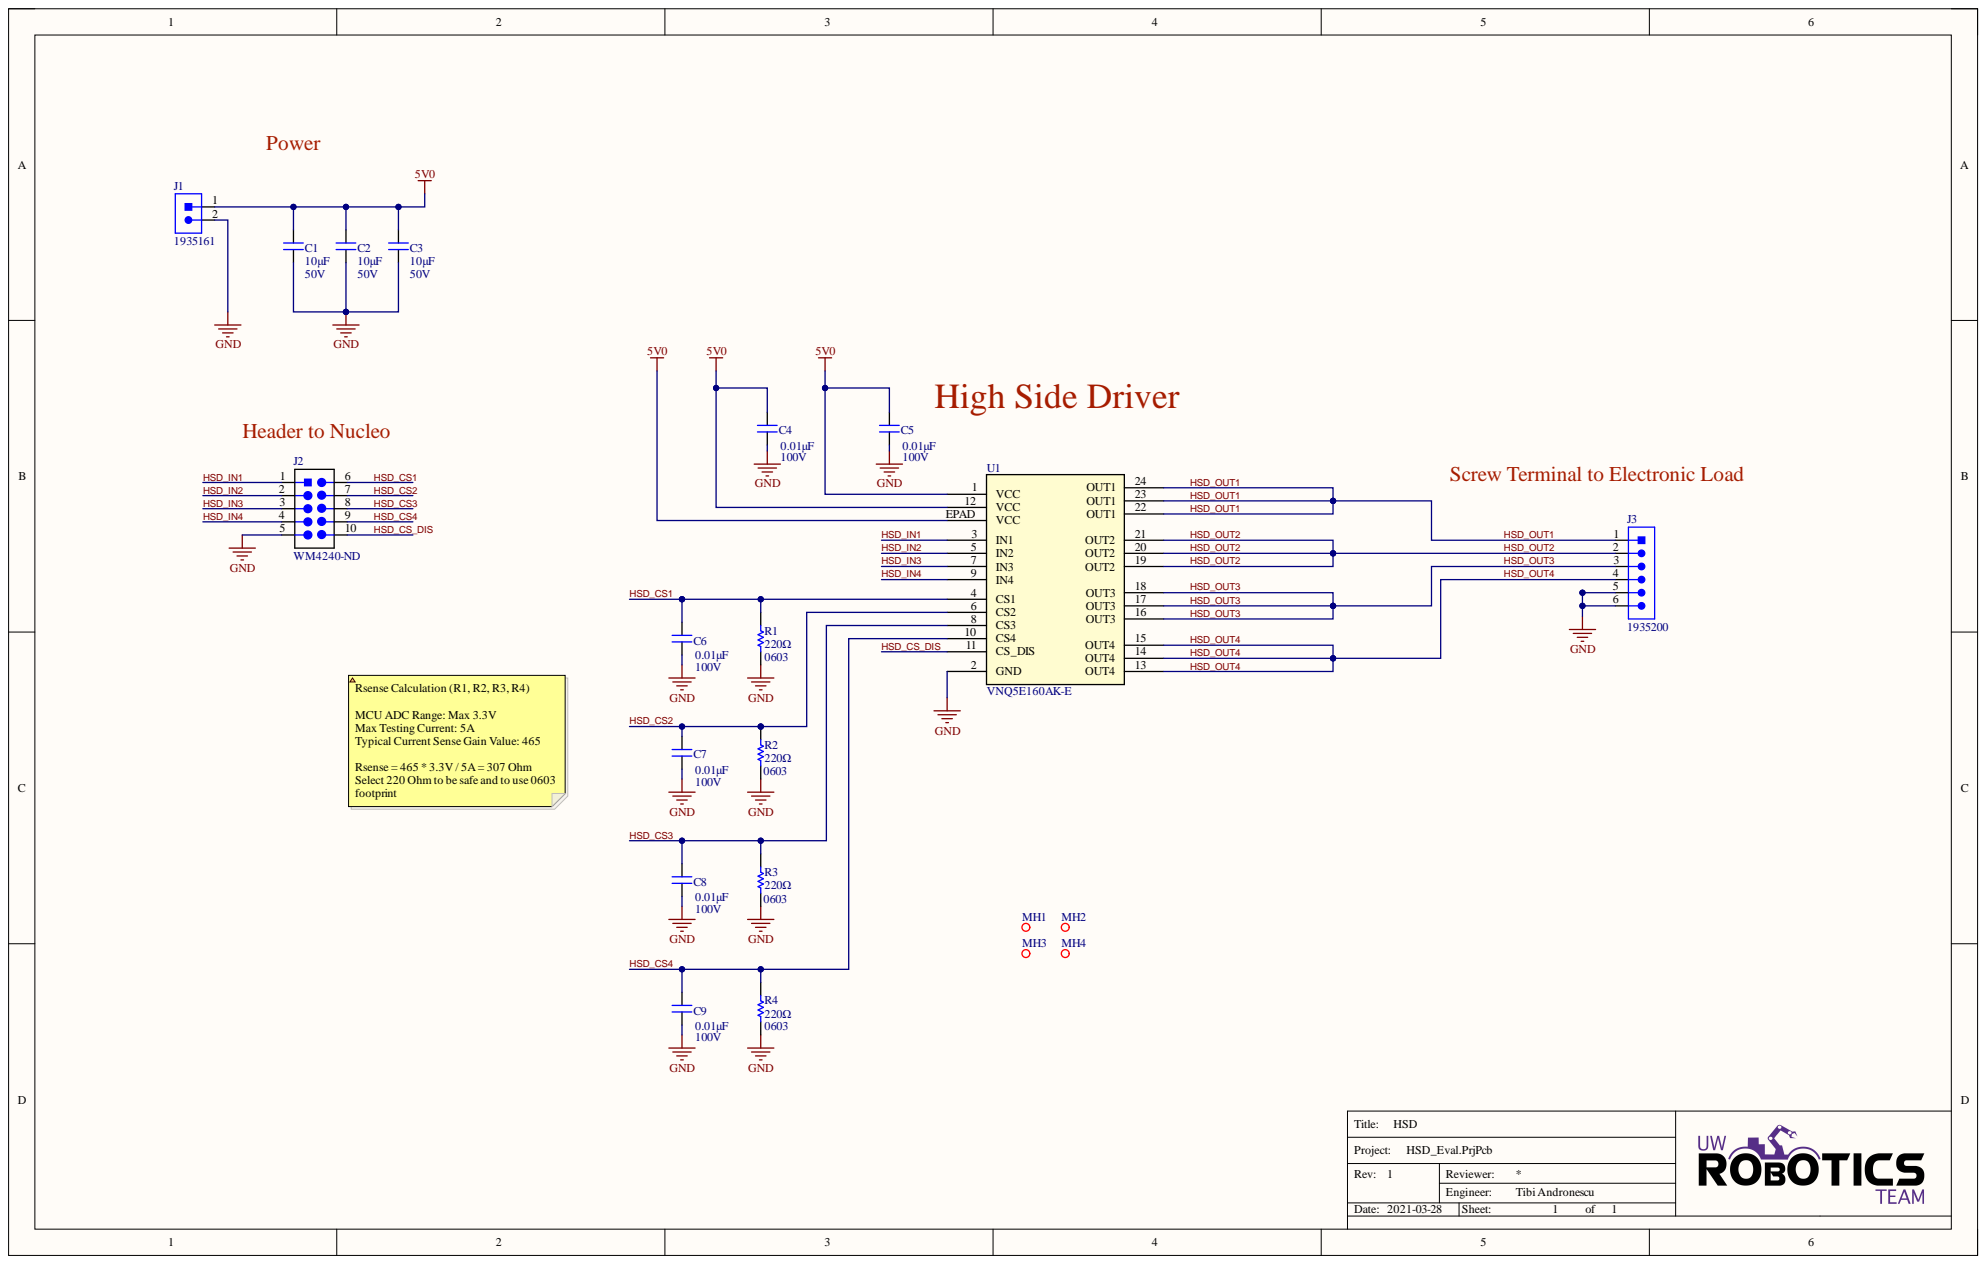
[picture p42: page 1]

23 OUT1 24 2 OUT1 | H S D _ O U T 1

VCC EPAD | H S D _ O U T 2

20 OUT2 21 9 OUT2 | H S D _ O U T 2 | H S D _ O U T 2

17 OUT3 18 6 OUT3 | H S D _ O U T 3

1 0 | | H S D _ O U T 4

14 OUT4 15 3 OUT4 | H S D _ O U T 4

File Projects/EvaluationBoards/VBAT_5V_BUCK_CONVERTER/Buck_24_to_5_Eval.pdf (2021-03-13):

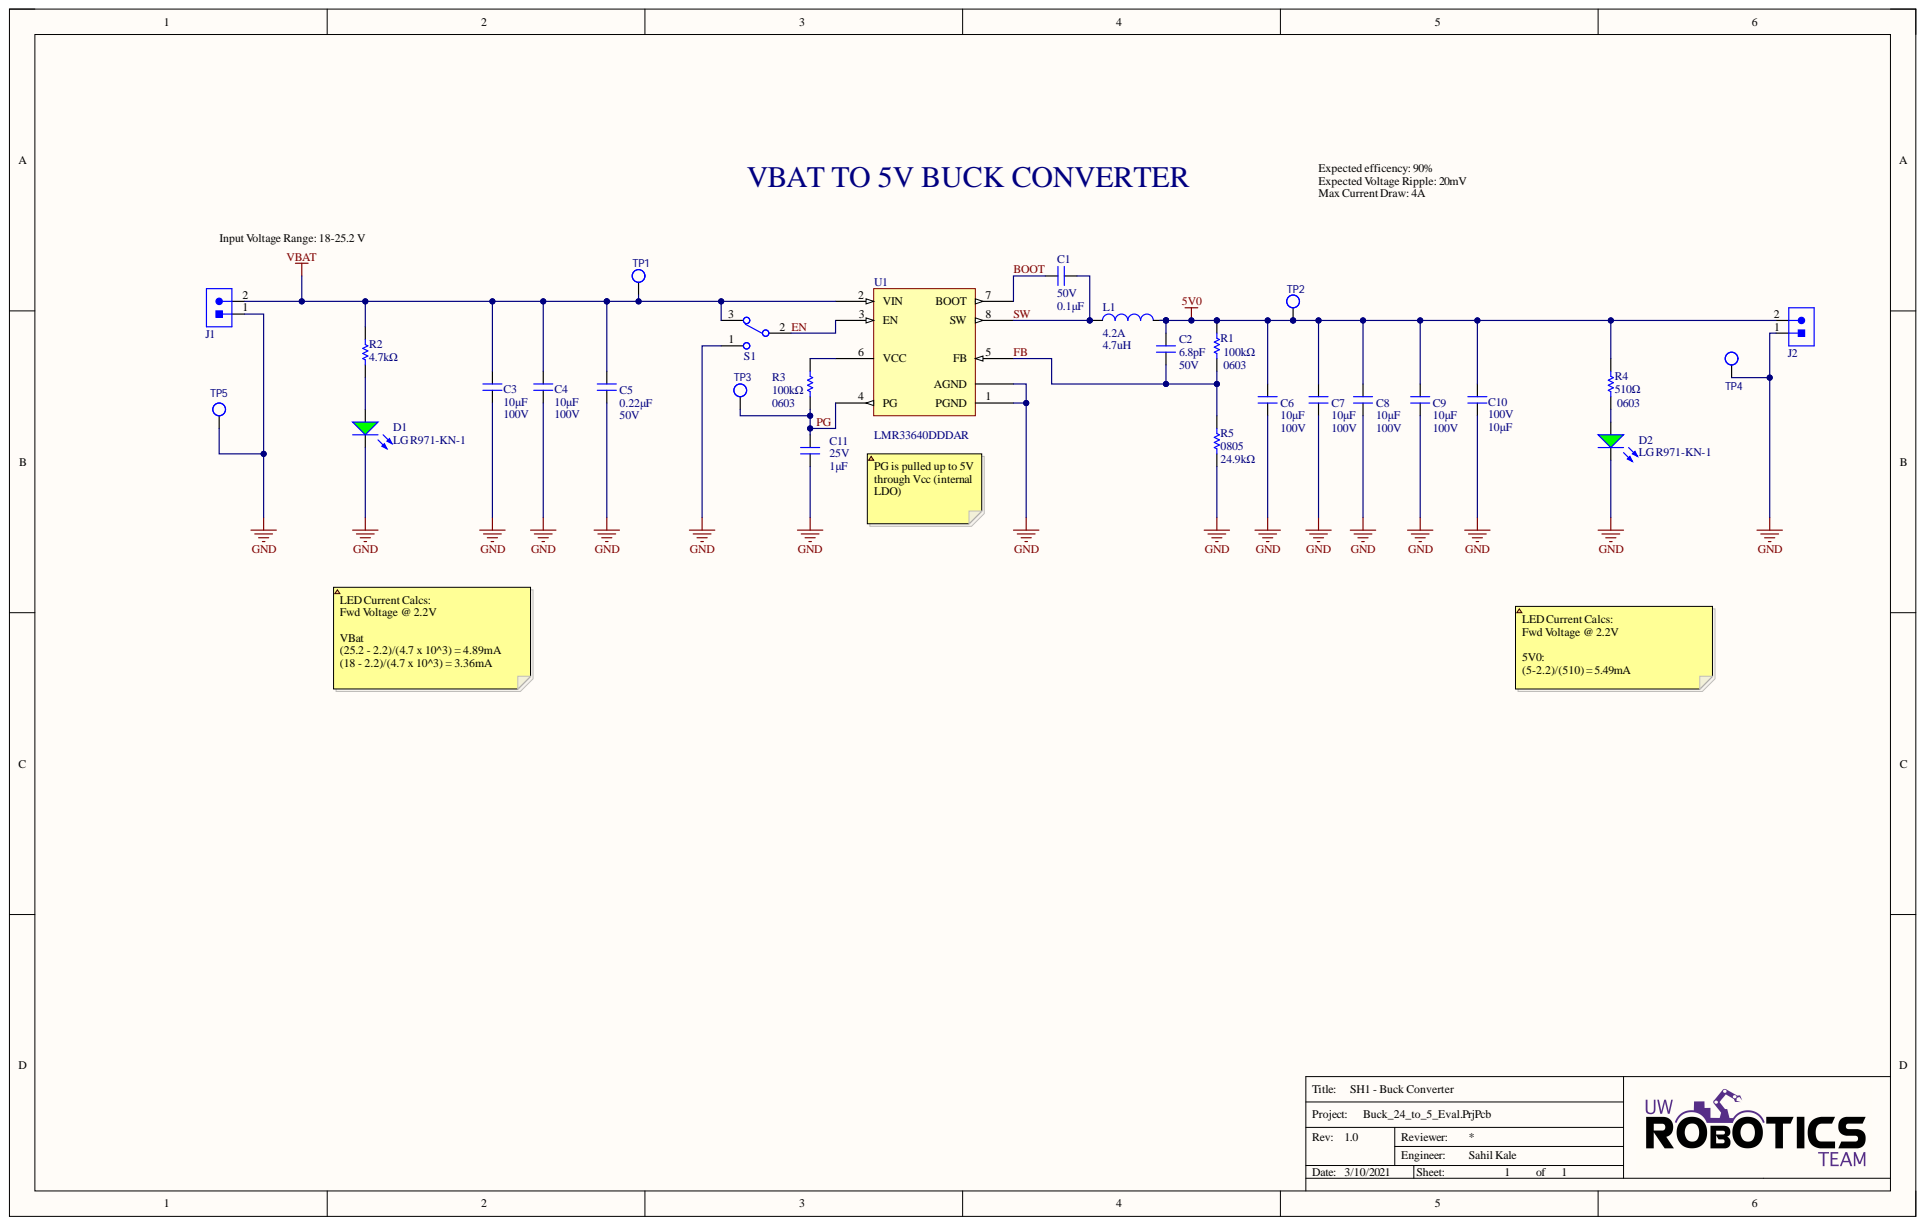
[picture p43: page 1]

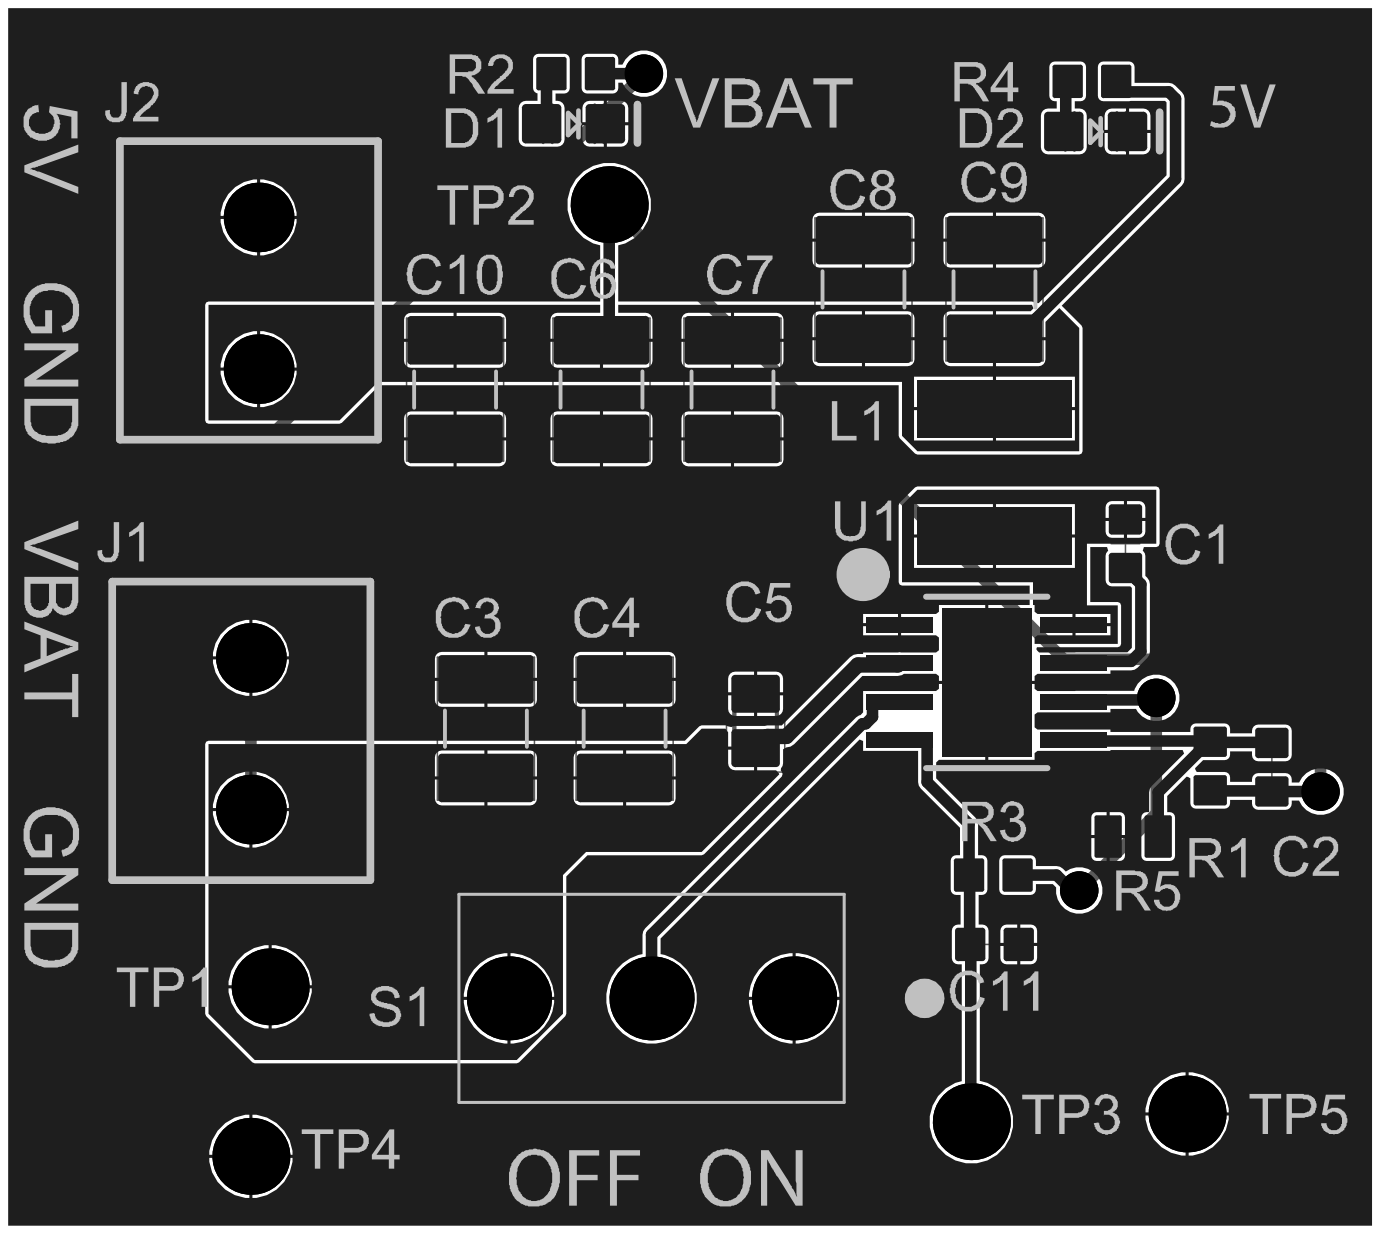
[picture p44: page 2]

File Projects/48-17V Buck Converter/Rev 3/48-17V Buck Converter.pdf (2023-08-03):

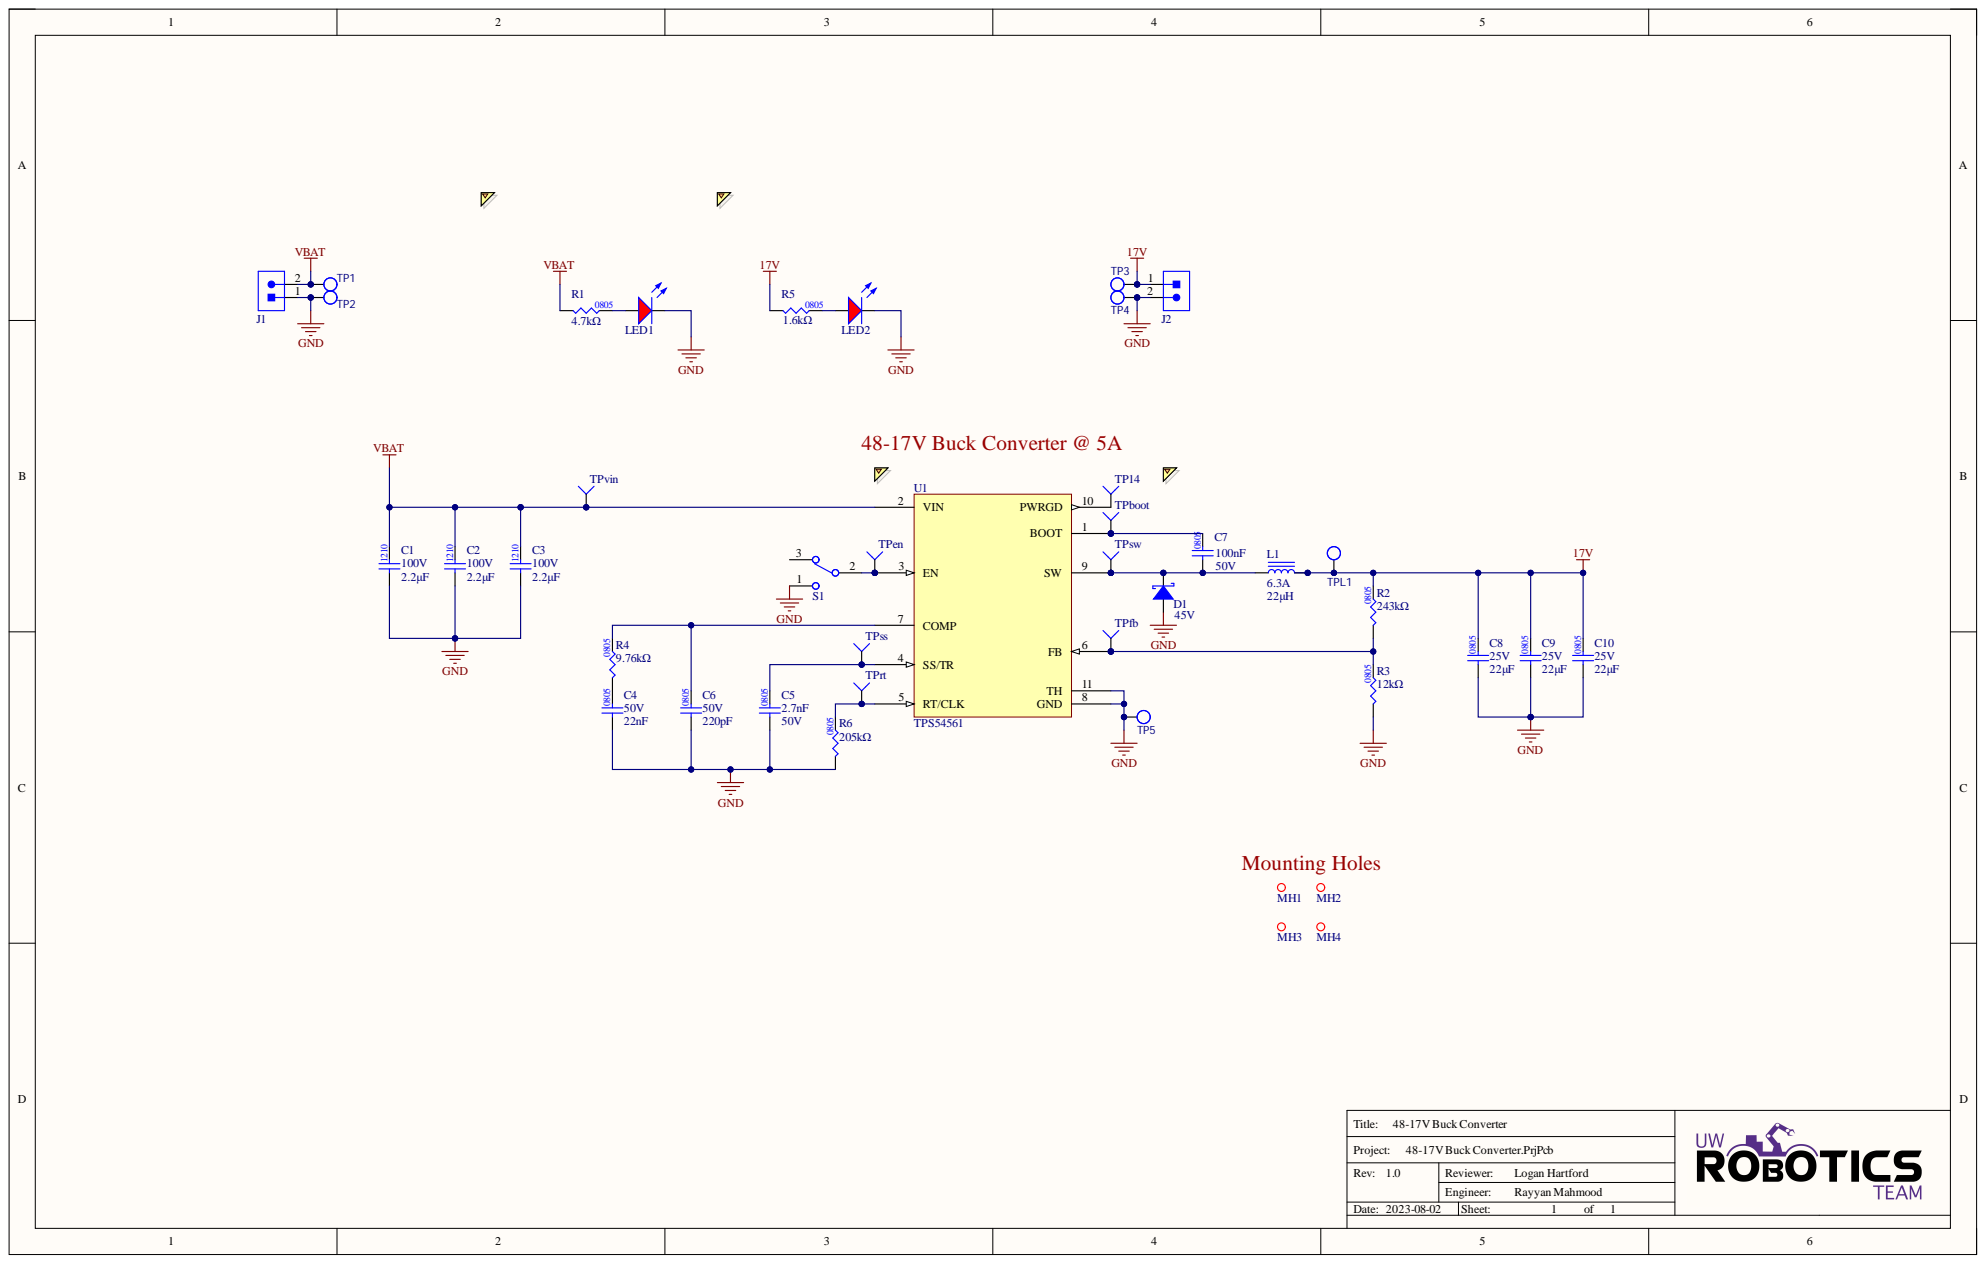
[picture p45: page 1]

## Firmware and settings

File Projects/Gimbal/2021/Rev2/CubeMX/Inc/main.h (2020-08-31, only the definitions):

#define LIM_GIMB_Pin GPIO_PIN_13
#define LIM_GIMB_GPIO_Port GPIOC
#define LED_1_Pin GPIO_PIN_0
#define LED_1_GPIO_Port GPIOC
#define LED_2_Pin GPIO_PIN_1
#define LED_2_GPIO_Port GPIOC
#define LED_3_Pin GPIO_PIN_2
#define LED_3_GPIO_Port GPIOC
#define LED_4_Pin GPIO_PIN_3
#define LED_4_GPIO_Port GPIOC
#define LED_MTRX_Pin GPIO_PIN_2
#define LED_MTRX_GPIO_Port GPIOA
#define ENC_GIMB_Pin GPIO_PIN_3
#define ENC_GIMB_GPIO_Port GPIOA
#define BUTTON_1_Pin GPIO_PIN_0
#define BUTTON_1_GPIO_Port GPIOB
#define BUTTON_2_Pin GPIO_PIN_1
#define BUTTON_2_GPIO_Port GPIOB
#define CAN_RX_2_Pin GPIO_PIN_12
#define CAN_RX_2_GPIO_Port GPIOB
#define CAN_TX_2_Pin GPIO_PIN_13
#define CAN_TX_2_GPIO_Port GPIOB
#define PWM_CR_Pin GPIO_PIN_14
#define PWM_CR_GPIO_Port GPIOB
#define PWM_MG_Pin GPIO_PIN_15
#define PWM_MG_GPIO_Port GPIOB
#define CAN_RX_1_Pin GPIO_PIN_11
#define CAN_RX_1_GPIO_Port GPIOA
#define CAN_TX_1_Pin GPIO_PIN_12
#define CAN_TX_1_GPIO_Port GPIOA
#define SWD_IO_Pin GPIO_PIN_13
#define SWD_IO_GPIO_Port GPIOA
#define SWD_CLK_Pin GPIO_PIN_14
#define SWD_CLK_GPIO_Port GPIOA
#define UART_TX_Pin GPIO_PIN_10
#define UART_TX_GPIO_Port GPIOC
#define UART_RX_Pin GPIO_PIN_11
#define UART_RX_GPIO_Port GPIOC
#define ULTRA_1_TRIG_Pin GPIO_PIN_6
#define ULTRA_1_TRIG_GPIO_Port GPIOB
#define ULTRA_1_ECHO_Pin GPIO_PIN_7
#define ULTRA_1_ECHO_GPIO_Port GPIOB
#define ULTRA_2_TRIG_Pin GPIO_PIN_8
#define ULTRA_2_TRIG_GPIO_Port GPIOB
#define ULTRA_2_ECHO_Pin GPIO_PIN_9
#define ULTRA_2_ECHO_GPIO_Port GPIOB

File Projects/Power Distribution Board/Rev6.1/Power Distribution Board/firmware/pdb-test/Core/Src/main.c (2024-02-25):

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
/* Includes ------------------------------------------------------------------*/
#include "main.h"

ADC_HandleTypeDef hadc1;
DMA_HandleTypeDef hdma_adc1;

CAN_HandleTypeDef hcan1;
CAN_HandleTypeDef hcan2;

RTC_HandleTypeDef hrtc;

TIM_HandleTypeDef htim3;
TIM_HandleTypeDef htim4;

void SystemClock_Config(void);
static void MX_GPIO_Init(void);
static void MX_DMA_Init(void);
static void MX_ADC1_Init(void);
static void MX_CAN1_Init(void);
static void MX_CAN2_Init(void);
static void MX_RTC_Init(void);
static void MX_TIM3_Init(void);
static void MX_TIM4_Init(void);
/**
  * @brief  The application entry point.
  * @retval int
  */
int main(void)
{
  /* MCU Configuration--------------------------------------------------------*/

  /* Reset of all peripherals, Initializes the Flash interface and the Systick. */
  HAL_Init();

  /* Configure the system clock */
  SystemClock_Config();

  /* Initialize all configured peripherals */
  MX_GPIO_Init();
  MX_DMA_Init();
  MX_ADC1_Init();
  MX_CAN1_Init();
  MX_CAN2_Init();
  MX_RTC_Init();
  MX_TIM3_Init();
  MX_TIM4_Init();
  /* USER CODE BEGIN 2 */
  HAL_GPIO_WritePin(GPIOC, EN_5V1_1_Pin, GPIO_PIN_SET);
  HAL_GPIO_WritePin(GPIOB, EN_5V1_2_Pin, GPIO_PIN_SET);
  HAL_GPIO_WritePin(GPIOC, EN_5V2_1_Pin, GPIO_PIN_SET);
  HAL_GPIO_WritePin(GPIOD, EN_5V2_2_Pin, GPIO_PIN_SET);
  HAL_GPIO_WritePin(GPIOB, EN_17V_Pin, GPIO_PIN_SET);
  HAL_GPIO_WritePin(GPIOC, EN_ODRIVE_1_Pin, GPIO_PIN_SET);
  HAL_GPIO_WritePin(GPIOC, EN_ODRIVE_2_Pin, GPIO_PIN_SET);
  HAL_GPIO_WritePin(GPIOA, EN_ODRIVE_3_Pin, GPIO_PIN_SET);
  HAL_GPIO_WritePin(GPIOC, EN_VBAT_BUCK_Pin, GPIO_PIN_SET);
  /* USER CODE END 2 */

  /* Infinite loop */
  /* USER CODE BEGIN WHILE */
  while (1)
  {
    /* USER CODE END WHILE */

    /* USER CODE BEGIN 3 */
	  GPIO_PinState fault_1_1_status = HAL_GPIO_ReadPin(GPIOC, FAULT_5V1_1_Pin);
	  if(fault_1_1_status == GPIO_PIN_RESET) {
	      	  HAL_GPIO_WritePin(GPIOC, EN_5V1_1_Pin, GPIO_PIN_RESET);
	  }
	  GPIO_PinState fault_1_2_status = HAL_GPIO_ReadPin(GPIOB, FAULT_5V1_2_Pin);
	  if(fault_1_2_status == GPIO_PIN_RESET) {
	      	  HAL_GPIO_WritePin(GPIOB, EN_5V1_2_Pin, GPIO_PIN_RESET);
	  }
	  GPIO_PinState fault_2_1_status = HAL_GPIO_ReadPin(GPIOC, FAULT_5V2_1_Pin);
	  if(fault_2_1_status == GPIO_PIN_RESET) {
	      	  HAL_GPIO_WritePin(GPIOC, EN_5V2_1_Pin, GPIO_PIN_RESET);
	  }
	  GPIO_PinState fault_2_2_status = HAL_GPIO_ReadPin(GPIOC, FAULT_5V2_2_Pin);
	  if(fault_2_2_status == GPIO_PIN_RESET) {
	      	  HAL_GPIO_WritePin(GPIOD, EN_5V2_2_Pin, GPIO_PIN_RESET);
	  }
	  HAL_ADC_Start(&hadc1);
	  HAL_ADC_PollForConversion(&hadc1, HAL_MAX_DELAY);
	  uint32_t raw = HAL_ADC_GetValue(&hadc1);
	  raw = raw << 4;
	  raw = raw >> 4;
	  float voltage = (float)raw / 4096.0 * 3.3;
	  if (voltage > 3.0) {
		  HAL_GPIO_WritePin(GPIOB, EN_17V_Pin, GPIO_PIN_RESET);
	  }
	  /*port all adc using dma circular/

  }


  /* USER CODE END 3 */
}

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
/* USER CODE BEGIN 4 */
void HAL_ADC_ConvHalfCpltCallback(ADC_HandleTypeDef* hadc) {
//  HAL_GPIO_WritePin(LD2_GPIO_Port, LD2_Pin, GPIO_PIN_SET);
	/*switch case based on input*/
}

/* USER CODE END 4 */
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


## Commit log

2020-11-02 LIBRARIES: fix crystal footprint
2020-11-02 LIBRARIES: fix 3.3V TVS diode footprint
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2020-11-02 LIBRARIES: fixed up footprint
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2020-11-02 HPBMC: add 17V linear regulator, change test points
    [High Power Brushed DC MC.PrjPcb, SH1 - CONNECTORS AND POWER.SchDoc, SH2 - MOTOR CONTROLLER.SchDoc]
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2020-11-03 PDB: Add decoupling caps, modify test point and zener diode placement
    [SH1 - POWER.SchDoc, SH10 - USB.SchDoc, SH11 - CAN.SchDoc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]
2020-11-03 LIBRARIES: fix 24V TVS diode text
2020-11-04 PDB: Replace TVS diode, caps, level shifter; modify comments
    [Power Distribution Board.PrjPcb, SH1 - POWER.SchDoc, SH10 - USB.SchDoc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]
2020-11-04 PDB: Fix caps
    [SH1 - POWER.SchDoc, SH10 - USB.SchDoc, SH11 - CAN.SchDoc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]
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2020-11-04 PDB: Flip CAN transceivers
    [SH11 - CAN.SchDoc]
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2020-11-06 ARMV2: remove buffer and jumpers from FSR circuit
    [SH8 - FORCE SENSITIVE RESISTOR.SchDoc]
2020-11-06 ARMV2: replace 3v3 buck with LDO
    [SH1 - POWER.SchDoc]
2020-11-06 LIBRARY/ARM: replace 125mA fuse component with the one in stock
    [SH2 - CONNECTORS_1.SchDoc, SH3 - CONNECTORS_2.SchDoc, SH4 - SPI ENCODERS.SchDoc]
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2020-11-07 PDB: Apply schematic fixes
    [Power Distribution Board.PrjPcb, SH1 - POWER.SchDoc, SH10 - USB.SchDoc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]
2020-11-07 LIBRARIES: Fix footprint links for caps; PDB: Create PcbDoc
    [Power Distribution Board.PrjPcb, SH1 - POWER.SchDoc, SH10 - USB.SchDoc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]
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2020-11-09 CONTROLLER: fix issues from schematic review
    [Arm.PrjPcb, GimbDrive.PrjPcb, SH1-MCU.SchDoc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]
2020-11-09 ARMV2: make level shifters page and move SPI level shifters there
    [Arm.PrjPcb, SH4 - SPI ENCODERS.SchDoc, SH9 - LEVEL SHIFTERS.SchDoc]
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2020-11-09 PDB: Add more schematic fixes
    [Power Distribution Board.PrjPcb, SH1 - POWER.SchDoc, SH10 - USB.SchDoc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]
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2020-11-10 CONTROLLER: update debug headers and remove unnecessary LEDs
    [Arm.PrjPcb, GimbDrive.PrjPcb, SH1-POWER.SchDoc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]
2020-11-11 LIBRARY: fix 24 pin connector footprint
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2020-11-11 ARMV2: add 100 pin MCU to the library
    [SH6 - MICROCONTROLLER.SchDoc]
2020-11-11 CONTROLLER: update USB circuit and add RPP schottky diodes
    [Arm.PrjPcb, GimbDrive.PrjPcb, SH1-POWER.SchDoc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]
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2020-11-12 ARMV2: change sheet structure, add fuse to 5V rail
    [Arm.PrjPcb, Current Sensor.SchDoc, SH2 - CONNECTORS_1.SchDoc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]
2020-11-13 CONTROLLER: fix redundant TVS diodes
    [SH1-POWER.SchDoc, SH2-MCU.SchDoc, SH3-USB AND UART.SchDoc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]
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2020-11-13 PDB: Fix schematics and parts
    [Power Distribution Board.PrjPcb, SH1 - POWER.SchDoc, SH10 - CAN.SchDoc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]
2020-11-14 PDB: Replace MOSFETs, test points, and tweak component placement
    [SH1 - POWER.SchDoc, SH10 - CAN.SchDoc, SH11 - RS-485.SchDoc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]
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2020-11-14 LIBS: fix adrianna's PDB 3d models: vicor and big fuse
2020-11-14 PDB: Replace ideal diode output cap
    [SH1 - POWER.SchDoc]
2020-11-15 LIBRARIES: Add LDO_3.3V_600mA, TVS_DIODE_BIDIR_26V; PDB: Remove a bunch of caps, replace TVS diode, swap test points, restructure schematics
    [Power Distribution Board.PrjPcb, SH1 - POWER.SchDoc, SH10 - CAN.SchDoc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]
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2020-11-15 ARMV2: fix power supply and termination of RS485 transceivers
    [Arm.PrjPcb, SH1 - POWER.SchDoc, SH5 - NETZER ENCODERS.SchDoc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]
2020-11-15 ARMV2/LIB: apply schematic review, fix footprint of 14pF cap
    [SH1 - POWER.SchDoc, SH2 - CONNECTORS_1.SchDoc, SH3 - CONNECTORS_2.SchDoc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]
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2020-11-16 PDB: Add Vbat connectors, apply schematic and placement fixes
    [SH1 - POWER.SchDoc, SH10 - RS-485.SchDoc, SH2 - 24V BUCK-BOOST CONVERTER.SchDoc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]
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2020-11-17 PDB: replace all 0603 passives with 0805
    [Power Distribution Board.PrjPcb, SH1 - POWER.SchDoc, SH10 - RS-485.SchDoc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]
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2020-11-17 LIBS: fix diode polarity footprints
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2020-11-17 LIBS: fix more diodes
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2020-11-17 PDB: update LED and 3.3V TVS diode footprints
    [Power Distribution Board.PrjPcb]
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2020-11-18 LOCALIZATION: fix project structure
    [Localization.PrjPcb]
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2020-11-18 CONTROLLER: create schematics and CubeMX for a single, large controller board
    [CompleteController.PrjPcb, SH1 - POWER.SchDoc, SH2 - MCU.SchDoc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]
2020-11-18 LIBS: fix SO-16N footprint
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2020-11-19 LIBS: fix LED footprints
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2020-11-20 ARMV2: change 1uF cap component and display cap ceramic type
    [SH1 - POWER.SchDoc, SH5 - NETZER ENCODERS.SchDoc, SH6 - MICROCONTROLLER.SchDoc]
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2020-11-20 ARMV2: add 33ohm series termination resistor to SPI output
    [Arm.PrjPcb, SH1 - POWER.SchDoc, SH2 - CONNECTORS_1.SchDoc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]
2020-11-20 ARMV2: replace 120ohm resistor with higher power rating
    [SH1 - POWER.SchDoc, SH2 - CONNECTORS_1.SchDoc, SH3 - CONNECTORS_2.SchDoc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]
2020-11-20 ARMV2: add 0 ohm resistor net tie between 3v3 and FSR_1
    [SH2 - CONNECTORS_1.SchDoc, SH8 - FORCE SENSITIVE RESISTOR.SchDoc]
2020-11-20 LIBS: fix broken footprint links
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2020-11-24 CONTROLLER: make minor tweaks to controller power sheet
    [SH1 - POWER.SchDoc]
2020-11-25 CONTROLLER: fix schematic components, start PCB layout
    [CompleteController.PrjPcb, SH1 - POWER.SchDoc, SH2 - MCU.SchDoc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]
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2020-11-28 CONTROLLER: change USB LED and work on layout
    [CompleteController.PrjPcb, SH3 - USB.SchDoc, SH4 - GIMBDRIVECONTROLS.SchDoc]
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2020-11-30 LIBS: replace out of stock 8A fuse
2020-11-30 LPMC: replace 8A fuse with 5A fuse
    [Low Power Brushed Motor Controller.PcbDoc, Low Power Brushed Motor Controller.PrjPcb, Low Power Brushed Motor Controller.SchDoc]
2020-11-30 LIBS: fix 270uF aluminum cap footprint
2020-11-30 LPMC: fix schematic
    [Low Power Brushed Motor Controller.PcbDoc, Low Power Brushed Motor Controller.PrjPcb, Low Power Brushed Motor Controller.SchDoc]
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2020-12-01 Update SH3 - NUCLEO HEADERS.SchDoc
    Reflect the true pinout; source: https://os.mbed.com/platforms/ST-Nucleo-F446RE/
    [SH3 - NUCLEO HEADERS.SchDoc]
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2020-12-02 LPMC: fix silkscreen
    [Low Power Brushed Motor Controller.PcbDoc]
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2020-12-03 NUCLEO SHIELD: Connected SPI pins
    SPI1 is now for the BISS encoder
    SPI2 is now for the SD card reader
    SPI3 will be for the broadcom encoder (not yet designated). Ports are made for it
    [SH2 - RS-485.SchDoc, SH3 - NUCLEO HEADERS.SchDoc, SH4 - SD CARD.SchDoc]
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2020-12-05 PDB: fix BOM
    [Power Distribution Board BOM.xlsx]
2020-12-05 PDB: fix gerbers
    [Power Distribution Board.GBO]
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2020-12-07 GIMBAL: fix PCBWay BOM
    [Gimbal BOM PCBWay.xlsx]
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2020-12-15 PDB: Apply review fixes
    [SH10 - RS-485.SchDoc, SH2 - 24V BUCK-BOOST CONVERTER.SchDoc, SH3 - 17V BUCK CONVERTER.SchDoc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]
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2020-12-19 LIBRARIES: Fix footprint pads
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2020-12-21 PDB: Fix schematic text and smart PDF
    [SH7 - LOAD MONITORING 2.SchDoc]
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2020-12-26 NUCLEO SHIELD: Fix connectors
    [SH2 - RS-485.SchDoc, SH3 - NUCLEO HEADERS.SchDoc, SH4 - SD CARD.SchDoc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]
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2020-12-29 LIBRARIES: Added a designator to IC Bidirectional Level Shifter (two channels) footprint
    [Nucleo Shield.PcbDoc, Nucleo Shield.PrjPcb, SH6 - BRUSHED MOTOR CONTROLLER.SchDoc]
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2021-01-02 CONTROLLER: address some issues from routing review
    [Robot Controller.PrjPcb, SH1 - POWER.SchDoc, SH2 - MCU.SchDoc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]
2021-01-03 CONTROLLER: fix some routing issues from review
    [Robot Controller.PrjPcb, SH2 - MCU.SchDoc]
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2021-01-10 CONTROLLER: fix most remaining issues from routing review
    [SH2 - MCU.SchDoc, SH4 - GIMBDRIVE CONTROLS.SchDoc, SH5 - ARM CONTROLS.SchDoc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]
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2021-01-23 CONTROLLER: fix remaining issues with layout from new review
    [Robot Controller.PrjPcb]
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2021-02-10 CONTROLLER: fix some issues with Controller CubeMX file
    [Robot Controller.ioc]
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2021-03-09 EVAL Boards: Fix placement of feedback resistor
    [SH1 - Buck Converter.SchDoc]
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2021-03-10 LIBS: Fix Footprint issue
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2021-03-10 EVAL BOARD: Fix DRC issues
    [Buck_Eval_Board.PcbDoc]
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2021-03-22 LED MATRIX: continue layout
    - Add calculations to schematic
    - Fix footprints
    [LED Matrix.PrjPcb, LED Matrix.SchDoc]
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2021-03-28 LED MATRIX: fixed silkscreen & pad spacing
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2021-03-28 LIBRARY: fix spacing for silkscree and soldermask for CAP1206
2021-03-28 HSD EVAL: update layout with new CAP1206 footprint to fix DRC
    [SH1 - HSD.SchDoc]
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2021-04-03 LIBS: fixed footprint links for resistor symbols
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2021-04-12 CURRENT SENSOR: fixed errors and cleaned up layout
    [Current Sensor.PcbDoc]
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2021-04-15 LIBS: fixed broken supplier link for 6.04k resistor
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2021-04-17 JETSON CARRIER: fix harness / hierarchy issue
    [JETSON AGX CONNECTOR TOP SHEET.SchDoc, Jetson AGX Xavier Carrier Board.PrjPcb, M.2 E-KEY.SchDoc]
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2021-04-18 reset schematic designators
    [PCIe ETHERNET.SchDoc, RGMII ETHERNET.SchDoc]
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2021-04-27 JETSON CARRIER: minor fixes
    [CAN.SchDoc, GPIO AND SERIAL.SchDoc, HDMI.SchDoc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]
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2021-05-03 JETSON CARRIER: replace coupling caps with 0402
    [JETSON AGX NVHS.SchDoc, JETSON AGX UPHY.SchDoc]
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2021-05-24 LIBS: replaced 0201 capacitors with 0805 capacitors
    [48V-24V Buck Converter.PrjPcb]
2021-05-24 LIBS: replaced 0201 and 0402 resistors with 0805 resistors
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2021-05-24 JETSON CARRIER: fix hdmi schematic
    [HDMI.SchDoc, JTAG.SchDoc]
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2021-05-29 LIBS: fixed NMOS footprint D-PAK3
2021-05-29 LIBS: fixed HTSSOP footprint
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2021-06-02 48V-24V BUCK: adjusted layout, replaced FETs
    [48V-24V Buck Converter.PrjPcb, Buck Converter.PcbDoc, Buck Converter.SchDoc]
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2021-06-12 48V-24V BUCK: replaced 0603 resistors with 0805
    [Buck Converter.PcbDoc, Buck Converter.SchDoc]
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2021-06-12 48V-24V BUCK: fixed folder structure
    [48V-24V Buck Converter.PrjPcb, Buck Converter.PcbDoc, Buck Converter.SchDoc]
2021-06-13 48V-24V BUCK: updated buck footprint & fixed wiring
    [Buck Converter.PcbDoc]
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2021-06-26 LIBS: fixed LM5117PWP buck schematic symbol
2021-06-26 LIBS: replaced 100uF capacitor
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2021-06-30 48V-24V BUCK: fixed file names
    [48V-24V Buck Converter.PcbDoc, 48V-24V Buck Converter.PrjPcb, 48V-24V Buck Converter.SchDoc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]
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2021-07-06 LIBS: replaced 22uF capacitor & fixed footprint
2021-07-06 48V-24V BUCK: replaced 22uF caps, minor revisions
    [48V-24V Buck Converter.PcbDoc, 48V-24V Buck Converter.PrjPcb, 48V-24V Buck Converter.SchDoc]
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2021-07-06 LIBS: replaced 54.9k out of stock resistor
    [48V-24V Buck Converter.SchDoc]
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2021-07-08 48V-24V BUCK: layout fix
    [48V-24V Buck Converter.PcbDoc]
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2021-07-11 JETSON CARRIER: small fixes
    [1.2V POWER.SchDoc, 1.8V POWER.SchDoc, 3.3V POWER.SchDoc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]
2021-07-13 Fix system sheet
    [HIGH LEVEL DESIGN.SchDoc, System.SchDoc]
2021-07-14 fix RGMII
    [RGMII ETHERNET.SchDoc]
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2021-07-14 LIBS: replaced 22uF capacitor
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2021-07-26 JETSON CARRIER: apply review fixes
    [1.2V POWER.SchDoc, 1.8V POWER.SchDoc, 3.3V POWER.SchDoc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]
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2021-08-02 JETSON: Add Missing Footprints
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2021-08-02 LIBRARIES: Fix all capacitor symbols
2021-08-02 LIBRARIES: Begin fixing resistor symbols
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2021-08-02 JETSON CARRIER: Fix more things
    [HDMI.SchDoc, JETSON AGX CONNECTOR.SchDoc, JETSON AGX CSI-I2C-I2S.SchDoc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]
2021-08-02 JETSON CARRIER: Fix RGMII sheet
    [CAN.SchDoc, Debug UART.SchDoc, GPIO AND SERIAL.SchDoc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]
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2021-08-03 LIBRARIES: Fix more Jetson symbols
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2021-08-24 JETSON CARRIER: fix some of Tomas' comments
    [BLOCK DIAGRAM.SchDoc, BUCK CONVERTERS.SchDoc, CAN.SchDoc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]
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2021-08-28 LED CONTROLLER: Fix layout from comments
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2021-08-31 BLDC: Minor fixes
    [Main.SchDoc]
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2021-10-14 Jetson Carrier: Fix Buck Converter Schematic
    [BUCK CONVERTERS.SchDoc]
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2021-10-28 Added RS422 Breakout Board project files, as well as associated new footprints and symbols (Molex 11 pin SMD connector, SOD923 tvs footprint)
    [RS422 Breakout.PcbDoc, RS422 Breakout.PrjPcb, RS422 Breakout.SchDoc]
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2021-11-05 Added 200mA 3V3 Fixed LDO LDK120M33R
2021-11-05 Updated schematic to use receiver instead of transceiver and updated layout according - ready for design review
    [RS422 Breakout.PcbDoc, RS422 Breakout.PrjPcb, RS422 Breakout.SchDoc]
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2021-11-07 LIBS: replaced 100V 90A NMOS
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2021-11-14 LIBS: restored missing pushbutton footprint
2021-11-14 LIBS: restored missing radial capacitor footprint
2021-11-14 LIBS: restored missing diode & cap 2220 fooptrints
2021-11-14 LIBS: restored missing IC and inductor footprints
2021-11-14 LIBS: fixed 1kOhm resistor symbol
2021-11-14 LIBS: restored missing buck IC footprint
2021-11-14 LIBS: fixed footprint link for buffer IC
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2021-11-14 LIBS: fixed cap 2220 footprint link
2021-11-14 PDB: fixed schematic links to part library
    [Power Distribution Board.PrjPcb, SH1 - POWER.SchDoc, SH2 - 17V BUCK CONVERTER.SchDoc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]
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2021-11-17 LIBS: fixed schottky diode symbol & footprint
2021-11-17 LIBS: fixed 8-tssop-bj footprint
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2021-12-03 BMS: Add buzzer and reset button
    [BMS.SchDoc]
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2021-12-12 LIBS: fixed PMOS pin numbering
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2021-12-15 LIBS: fixed 8-VSSOP footprint
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2021-12-23 Schematic changes according to 11/05/2021 schematic design review comments. Complete board layout change corresponding to schematic changes. Main changes - Header to solder directly onto ODrive, chan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
    [RS422 Breakout.PrjPcb, RS422 Breakout.SchDoc]
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2021-12-30 Fixing Errors
    [BLOCK DIAGRAM.SchDoc, CAN.SchDoc, Debug UART.SchDoc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]
2021-12-30 Fix PCB file
2021-12-30 PDB: fixed up layout errors
    [Power Distribution Board.PrjPcb]
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2022-01-07 SPI LVDS Master and Slave projects - Master schematic ready for design review
    [SPI LVDS Master.PcbDoc, SPI LVDS Master.PrjPcb, SPI LVDS Master.SchDoc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]
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2022-01-12 Fix error on M.2 M Key Page
    [M.2 M-KEY.SchDoc]
2022-01-12 Fixed floating NO ERC Error on I2C Page
    [JETSON AGX CSI-I2C-I2S.SchDoc]
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2022-01-13 Added testpoints, increased clearance to 10mils, changed silkscreen text, added teardrops, avoided vias through silkscreen
    [RS422 Breakout.PrjPcb, RS422 Breakout.SchDoc]
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2022-01-15 SN65LVDS179MDGKREP Footprint Fixes
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2022-01-19 PDB: Fix BMS layout from feedback
    [Power Distribution Board.PrjPcb]
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2022-01-25 Fix usb nets
    [USB.SchDoc]
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2022-02-25 SPI LVDS Host Board: Replacement Molex Connector
    [SPI LVDS Master.PrjPcb]
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2022-05-07 science connector pad fix
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2022-07-11 LIBS: Added necessary components for PDB Rev4
    Added the components that will be used in PDB rev 4, still need to make some changes
    [Power Distribution Board.PrjPcb]
2022-07-11 LIBS: added components for REV4
    Added most of the components to the library for PDB rev 4
    [Power Distribution Board.PrjPcb]
2022-07-13 Made the Schematics for Rev 4 PDB: 5V Buck and 17 V Buck
    Schamatics for 5V Buck and 17 V buck are made, need to make new schematics/footprints for the missing components though
    [OdbCache.cfg, PDN Sample.PcbDoc, Pick Place for Power Distribution Board.csv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]
2022-07-16 Replaced necessary components on PDB
    Replace temp sensor, some diodes and fixed some supplier links
    [Power Distribution Board.PrjPcb, SH1 - POWER.SchDoc, SH10 - BMS.SchDoc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]
2022-07-17 Updated some parts
    Replaced COUT caps and P Channel FET
    [SH1 - POWER.SchDoc, SH2 - 17V BUCK CONVERTER.SchDoc, SH3 - 5V BUCK CONVERTER.SchDoc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]
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2022-07-19 added some more changes
    Fixed 17 V Buck
    [SH1 - POWER.SchDoc, SH2 - 17V BUCK CONVERTER.SchDoc, SH8 - CAN.SchDoc]
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2022-07-30 LIBS: Fixed the libraries for the PDB
    title
    [SH2 - 17V BUCK CONVERTER.SchDoc, SH3 - 5V BUCK CONVERTER.SchDoc]
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2022-08-16 Some schematic changes
    Edited the Schematics for 17V and 5V Buck Converters
    [SH2 - 17V BUCK CONVERTER.SchDoc, SH3 - 5V BUCK CONVERTER.SchDoc]
2022-08-16 another minor change
    fixed temp sensor
    [SH7 - MICROCONTROLLER.SchDoc]
2022-08-18 Minor 5V Buck change
    fixed the inductor on 5V Buck
    [SH3 - 5V BUCK CONVERTER.SchDoc]
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2022-08-18 pushing changes I missed last push
    [SH2 - 17V BUCK CONVERTER.SchDoc, SH3 - 5V BUCK CONVERTER.SchDoc]
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2022-08-26 Did some Layout stuff
    Also edited the schematics a bit on microcontroller
    [Power Distribution Board.PrjPcb, SH1 - POWER.SchDoc, SH10 - BMS.SchDoc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]
2022-08-26 pushing change again
    in case altium failed to push everything last time
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2022-09-01 Made edits to schematic and PCB
    Moved around some components on the PCB and fixed the diode
    [SH1 - POWER.SchDoc, SH2 - 17V BUCK CONVERTER.SchDoc, SH3 - 5V BUCK CONVERTER.SchDoc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]
2022-09-02 PDB changes
    Made minor changes to the PCB on the PDB and some schematic changes
    [SH1 - POWER.SchDoc, SH2 - 17V BUCK CONVERTER.SchDoc, SH3 - 5V BUCK CONVERTER.SchDoc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]
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2022-09-11 LIBS: Changed some out of stock components
    replaced some capacitors and some other parts
    [SH2 - 17V BUCK CONVERTER.SchDoc, SH3 - 5V BUCK CONVERTER.SchDoc, SH7 - MICROCONTROLLER.SchDoc]
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2022-09-20 Made some changes to PCB and minor library edits
    Fixed some of the 5 and 17 V buck connections and the footprints for certain caps
    [SH2 - 17V BUCK CONVERTER.SchDoc, SH3 - 5V BUCK CONVERTER.SchDoc]
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2022-09-24 Made changes to PDB Layout
    Moved most of the components onto the board, fixed CAN, moved screw terminals
    [SH1 - POWER.SchDoc, SH3 - 5V BUCK CONVERTER.SchDoc, SH8 - CAN.SchDoc]
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2022-09-26 reverted some changes to the PDB libraries
    Fixed some of the missing footprints + minor PDB PCB changes
    [SH2 - 17V BUCK CONVERTER.SchDoc, SH3 - 5V BUCK CONVERTER.SchDoc, SH7 - MICROCONTROLLER.SchDoc]
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2022-09-30 DRC to 0
    Fixed all Design rule check errors
    [SH2 - 17V BUCK CONVERTER.SchDoc]
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2022-10-01 Add text labels & missing cad models
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2022-10-08 fixing bms buck converter
    [Battery Management System Rev3.PrjPcb]
2022-10-08 final minor edits to PDB
    moved some designnators, moved Q1 and extended VBAT Fused
    [Power Distribution Board.PrjPcb, SH1 - POWER.SchDoc]
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2022-11-13 SPI PERIPHERAL: minor edits to layout & testpoints to prep for fab
    [SPI LVDS Peripheral.PrjPcb, SPI LVDS Peripheral.SchDoc]
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2023-01-18 More Layout changes to PDB rev 4.1
    Pretty much done layout for 5V buck
    Fixed some changes to 17 V Buck
    Pretty much all of the residue from the previous placement is gone
    Fixed the Inductor and Diode Footprints
    [SH2 - 17V BUCK CONVERTER.SchDoc, SH3 - 5V BUCK CONVERTER.SchDoc]
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2023-02-10 LIBS: added missing footprint on an 0603 cap
2023-02-10 RS422 BREAKOUT: created rev1.1, fixed minor issues from rev1 like small footprints and unnecessary parts
    [RS422 Breakout.GBL, RS422 Breakout.GBO, RS422 Breakout.GBP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]
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2023-04-27 fixed designators on 5v switch
    [SH1 - 48V POWER.SchDoc, SH2 - 5V POWER.SchDoc]
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2023-04-27 fixed smart switch footprint
    [SH2 - 5V POWER.SchDoc]
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2023-05-04 updates to missing footprints
    [48-17V Buck Converter.SchDoc]
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2023-05-11 Fixed an error in the current sense amplifier cirtuit
    [SH1 - 48V POWER.SchDoc, SH3 - 17V POWER.SchDoc, SH5 - MICROCONTROLLER.SchDoc]
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2023-05-11 found another error with the current amplifier
    [SH1 - 48V POWER.SchDoc, SH3 - 17V POWER.SchDoc, SH5 - MICROCONTROLLER.SchDoc]
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2023-06-02 Buck Layout Fix
    [48V-5V Buck.PcbDoc, 48V-5V Buck.PrjPcb]
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2023-06-02 48-17V buck layout with fixed silk screen info
    [48-17V Buck Converter.PcbDoc]
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2023-06-09 48-17V buck layout + meme fixed
    [48-17V Buck Converter.PcbDoc]
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2023-06-11 couple files were missing in previous push
    [48-17V Buck Converter.PrjPcb]
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2023-07-12 Added IC, diode, inductor, and passives to Buck schematic, added components to library
    [30to50V-24V.SchDoc]
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2023-07-13 Fixed design
    [30to50V-24V PDB.PrjPcb, 30to50V-24V_10A_1.SchDoc, 30to50V-24V_10A_2.SchDoc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]
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2023-07-15 Fixed some designs, updated library, added LEDs and MH's
    [30to50V-24V_10A_1.SchDoc, 30to50V-24V_10A_2.SchDoc, 30to50V-24V_10A_3.SchDoc]
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2023-07-17 Fixed title block
    [30to50V-24V_10A.SchDoc]
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2023-07-29 Copy of Rev5 since I made changes to rev 5 on my laptop by accident
    [Power Distribution Board Rev5.GBL, Power Distribution Board Rev5.GBO, Power Distribution Board Rev5.GBP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]
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2023-08-05 Fixed STM pin allocations
    [SH5 - MICROCONTROLLER.SchDoc]
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2023-08-05 fixing a mistake in symbol
    [SH2 - 5V POWER.SchDoc]
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2023-08-09 Fixed a cap footprint
    [SH2 - 5V POWER.SchDoc, SH5 - MICROCONTROLLER.SchDoc]
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2023-08-11 generated gerbers and fixed a diode footprint
    [Power Distribution Board Rev5.GBL, Power Distribution Board Rev5.GBO, Power Distribution Board Rev5.GBP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]
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2023-08-12 Made 5V buck rev2 schematic changes and fixed rev folders
    [48V-5V Buck.GBL, 48V-5V Buck.GBO, 48V-5V Buck.GBP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]
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2024-10-28 fix product parameter
    [MCU.SchDoc, Power.SchDoc]
2024-10-28 fix symbol style issue
    [MCU.SchDoc, Power.SchDoc]
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2024-10-28 style fix
    [Power.SchDoc]
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2025-06-09 Small fix on connectors
    [Gate_Driver_Connectors.SchDoc]

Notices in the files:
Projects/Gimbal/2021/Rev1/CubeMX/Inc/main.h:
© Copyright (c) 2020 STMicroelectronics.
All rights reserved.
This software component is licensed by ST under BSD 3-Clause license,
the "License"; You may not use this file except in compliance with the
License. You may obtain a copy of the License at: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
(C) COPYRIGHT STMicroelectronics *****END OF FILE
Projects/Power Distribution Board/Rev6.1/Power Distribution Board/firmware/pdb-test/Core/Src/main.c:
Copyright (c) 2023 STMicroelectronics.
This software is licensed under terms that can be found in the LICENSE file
